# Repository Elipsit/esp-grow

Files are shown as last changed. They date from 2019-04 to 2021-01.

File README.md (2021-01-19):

# esp-grow
## Project Description
This was a project designed to get fimilar with the ESP8266 and ESP32 chipset.

## esp-grow
### This was an esp8266 based automatic plant monitor system.
The system will monitor the capacitive soil sensor, tenperature and humidity and activate the water pump accordingly.
The system hosts its own webpage to give the user status of the plants progress.

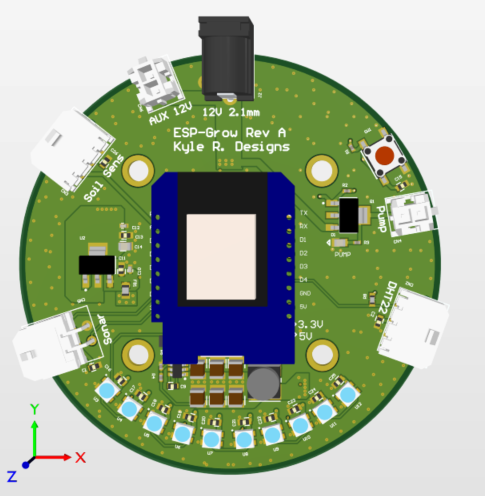
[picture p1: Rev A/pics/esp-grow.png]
esp-grow


custom soil sensor
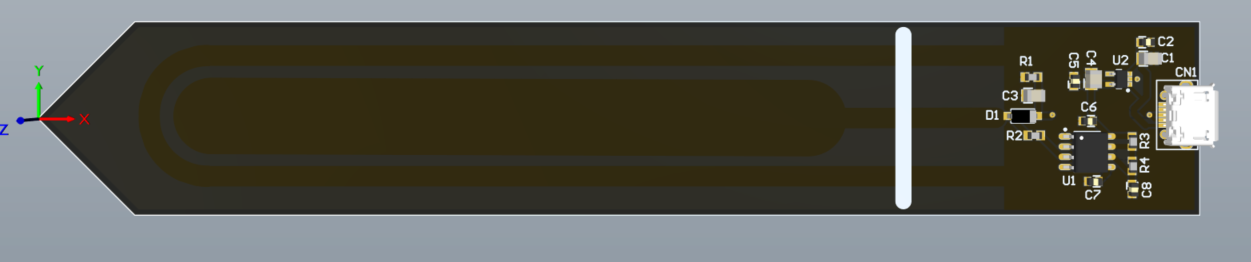
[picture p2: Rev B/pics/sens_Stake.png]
sens_stake


## Design Files
### Electrical Design Files
This project contains the Altium Designer schematic and pcb files, wiring diacrams and code for an esp8266 based indoor plant monitoring system.

This system is comprised of three main blocks:
1) Wemos D1 - ESP-12F; I really like working with this form factor since it has an esp8266 with a breadboard header and a CH340G
2) ESP-Grow_OLED_Rev_A: custom 2 layer pcb with a generic SSD1306 128x64 I2C monochrome OLED screen and a tack button seated under the screen.      Basically a screen button.
3) ESP-Grow_OLED_Main_A: The motherboard. A custom 4 Layer pcb with all the connectors, power rails and leds.

Update:
-DHT22 library has an error with ESP8266 and ESP32, changing to DHT11 for project sensor

###Current Progress: 5/18/2019
Project is functional. Rev A is retired.

## esp32-grow
### This was an esp32 based automatic plant monitor system.
This system was designed to monitor up to 50 plants at a time and upload the data to google firebase.
The device measures 50 capacitive soil sensors, air temperature, humidity and a single pH probe.

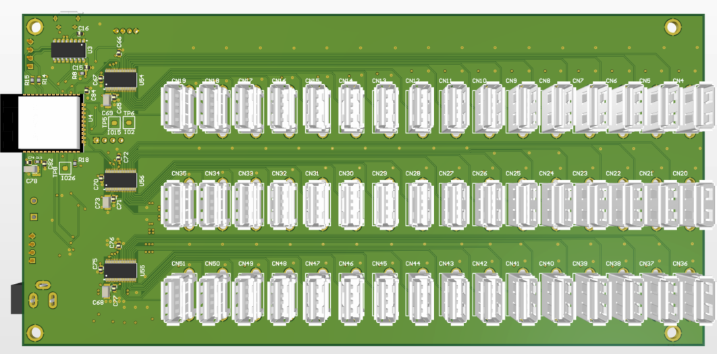
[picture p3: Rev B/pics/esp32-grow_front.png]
esp32-grow


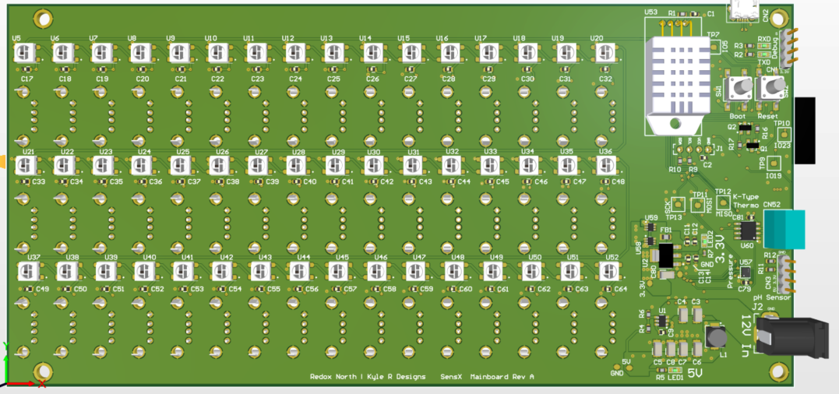
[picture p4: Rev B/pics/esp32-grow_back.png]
esp32-grow


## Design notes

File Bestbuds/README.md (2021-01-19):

# BestBuds
 Best Buds growing platform for ESP32

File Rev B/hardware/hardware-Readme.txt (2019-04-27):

All pcb design was done in Altium Designer 17 and Nexus

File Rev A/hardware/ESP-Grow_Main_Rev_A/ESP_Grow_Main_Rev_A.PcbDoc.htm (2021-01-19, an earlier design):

Reporting Options

# File in Previous Format

Date | : | 1/18/2021
Time | : | 10:08:27 PM
Filename | : | C:\github\esp-grow\Rev A\hardware\ESP-Grow_Main_Rev_A\ESP_Grow_Main_Rev_A.PcbDoc

Version | Warning

This file was generated by an earlier version of the software

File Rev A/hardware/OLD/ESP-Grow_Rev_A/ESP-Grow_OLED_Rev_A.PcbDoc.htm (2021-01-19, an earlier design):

Reporting Options

# File in Previous Format

Date | : | 6/29/2020
Time | : | 7:53:46 PM
Filename | : | C:\github\esp-grow\Rev A\hardware\OLD\ESP-Grow_Rev_A\ESP-Grow_OLED_Rev_A.PcbDoc

Version | Warning

This file was generated by an earlier version of the software

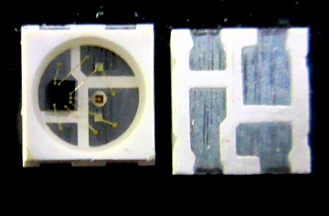
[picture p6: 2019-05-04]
Rev B/hardware/Datasheets/RGB/sk6812-sk6814-smd3535-1.snapshot.1/Capture0.PNG

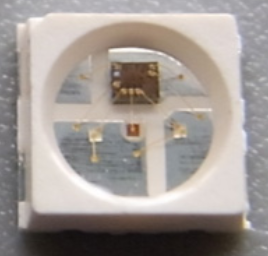
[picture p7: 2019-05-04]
Rev B/hardware/Datasheets/RGB/sk6812-sk6814-smd3535-1.snapshot.1/Capture2.PNG

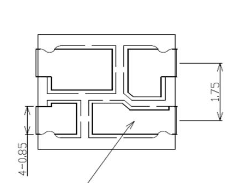
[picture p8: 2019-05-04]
Rev B/hardware/Datasheets/RGB/sk6812-sk6814-smd3535-1.snapshot.1/Capture1.PNG

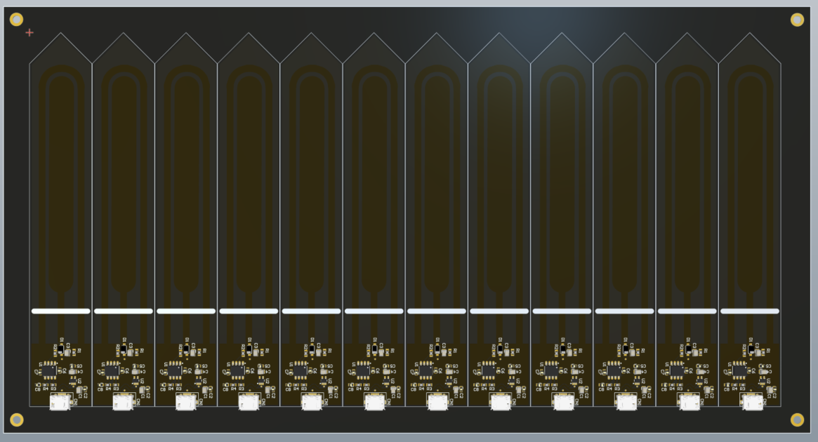
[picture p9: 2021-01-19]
Rev B/pics/Sens_Stake_panel.png

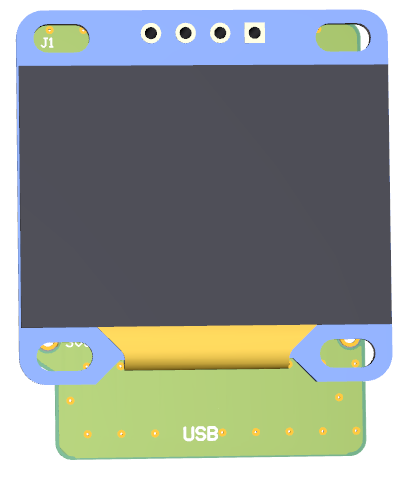
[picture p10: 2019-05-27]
Rev B/visio/ESP-Grow_OLED_Rev_A.1.PNG

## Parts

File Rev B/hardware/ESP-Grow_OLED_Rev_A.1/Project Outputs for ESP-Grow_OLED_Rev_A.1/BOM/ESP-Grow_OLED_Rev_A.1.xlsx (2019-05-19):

Line # | Name | Description | Designator | Quantity | Manufacturer 1 | Manufacturer Part Number 1 | Manufacturer Lifecycle 1 | Supplier 1 | Supplier Part Number 1 | Supplier Unit Price 1 | Supplier Subtotal 1
 | 0.1uF | CAP CER 0.1UF 50V 10% X7R 0805 | C1 | 1
 | J/Wemo_ESP_Shield | Wemo Mini Shield for ESP-12 | CN1 | 1
 | OLED 0.96" | SSD1306 I2C OLED 0.96" | J1 | 1
 | 10K | RES 10K OHM 1/10W 1% 0603 SMD | R1, R2, R3 | 3
 | PTS645SM43SMTR92 LFS | SWITCH TACTILE SPST-NO 0.05A 12V | SW1 | 1

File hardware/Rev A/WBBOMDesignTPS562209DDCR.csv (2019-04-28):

Part | Manufacturer | Part Number | Quantity | Price ($) | Footprint (mm²) | Description
Cin | TDK | C2012X6S1C226M125AC | 1 | 0.26 | 6.75 | Cap: 22 µF Total Derated Cap: 5.5 µF VDC: 16 V ESR: 2.05 mΩ Package: 0805
Rfbb | Yageo | RC0201FR-0710KL | 1 | 0.01 | 2.08 | Resistance: 10 kΩ Tolerance: 1.0% Power: 50 mW
U1 | Texas Instruments | TPS562209DDCR | 1 | 0.4 | 10.47
Cbst | Kemet | C0603C104Z3VACTU | 1 | 0.01 | 4.68 | Cap: 100 nF Total Derated Cap: 100 nF VDC: 25 V ESR: 1 mΩ Package: 0603
Cout | TDK | C1608X5R1A226M080AC | 1 | 0.13 | 4.68 | Cap: 22 µF Total Derated Cap: 4.5 µF VDC: 10 V ESR: 3.71 mΩ Package: 0603
L1 | Bourns | SRN6045-4R7Y | 1 | 0.2 | 64 | L: 4.7 µH DCR: 37.6 mΩ IDC: 3 A
Rfbt | Yageo | RC0201FR-0756K2L | 1 | 0.01 | 2.08 | Resistance: 56.2 kΩ Tolerance: 1.0% Power: 50 mW

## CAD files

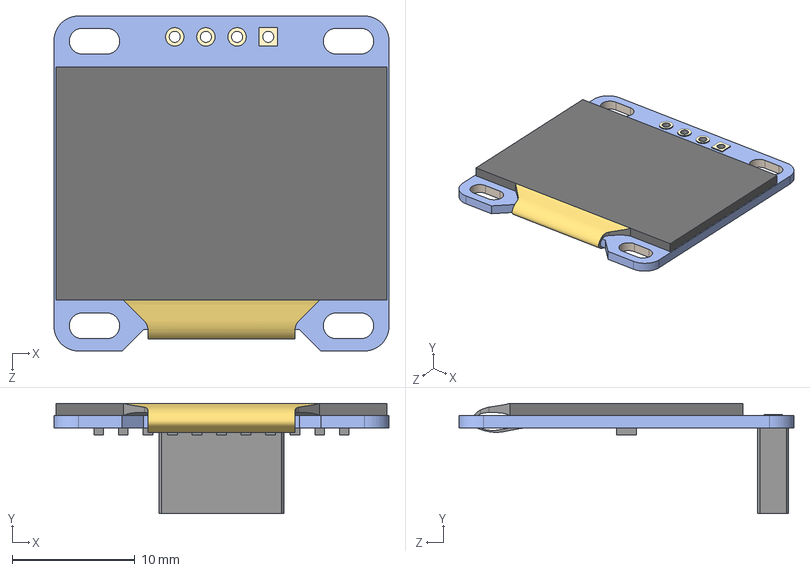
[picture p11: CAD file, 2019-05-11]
Rev B/hardware/Datasheets/OLED_27x27_r2.STEP
27.3 x 9.00 x 27.3 mm

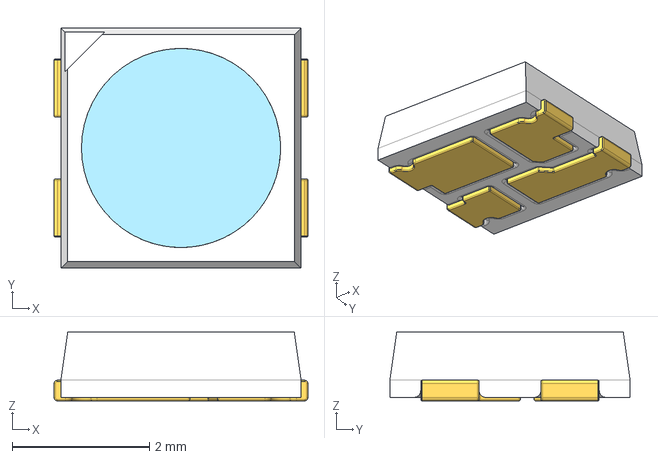
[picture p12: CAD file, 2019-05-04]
Rev B/hardware/Datasheets/RGB/sk6812-sk6814-smd3535-1.snapshot.1/SMD3535 RGB.stp
3.70 x 3.50 x 1.00 mm

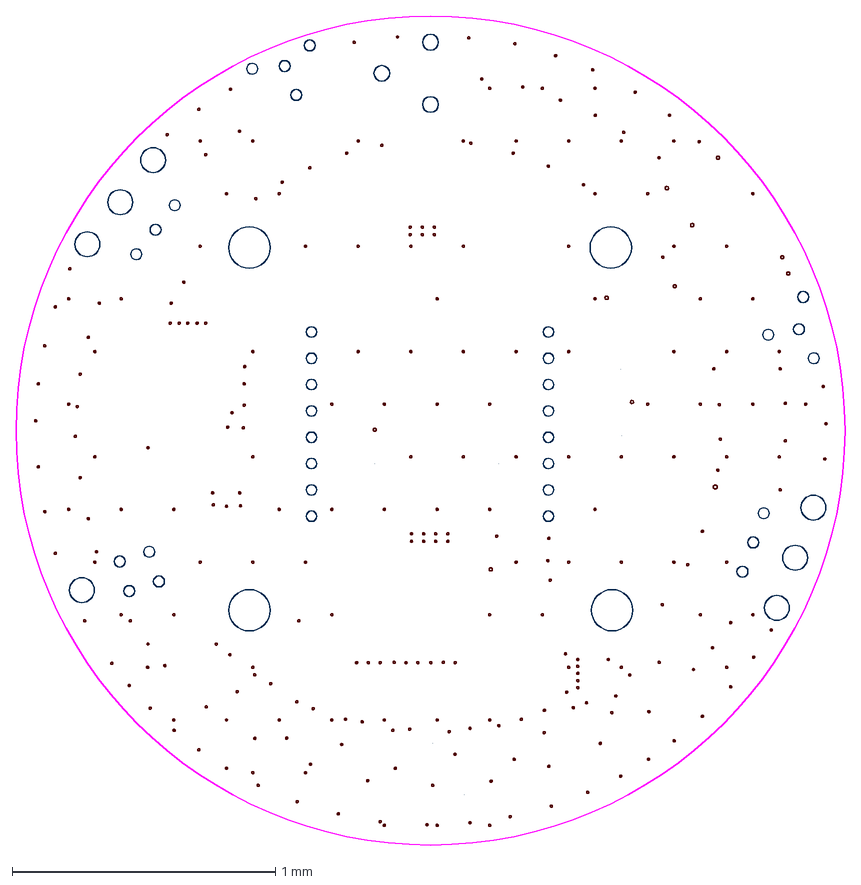
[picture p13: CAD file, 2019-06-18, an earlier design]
Rev A/mechanical/ESP_Grow_Main_Rev_A_Keepout.DXF
3.15 x 3.15 mm

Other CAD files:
Rev A/hardware/ESP-Grow_Main_Rev_A/ESP_Grow_Main_Rev_A.DXF

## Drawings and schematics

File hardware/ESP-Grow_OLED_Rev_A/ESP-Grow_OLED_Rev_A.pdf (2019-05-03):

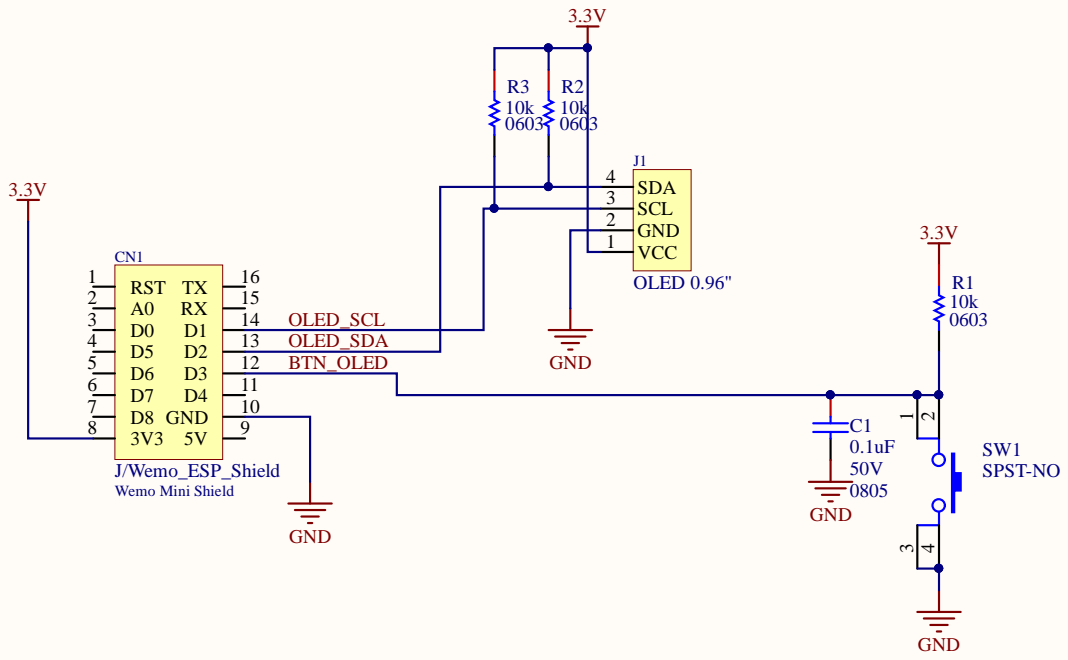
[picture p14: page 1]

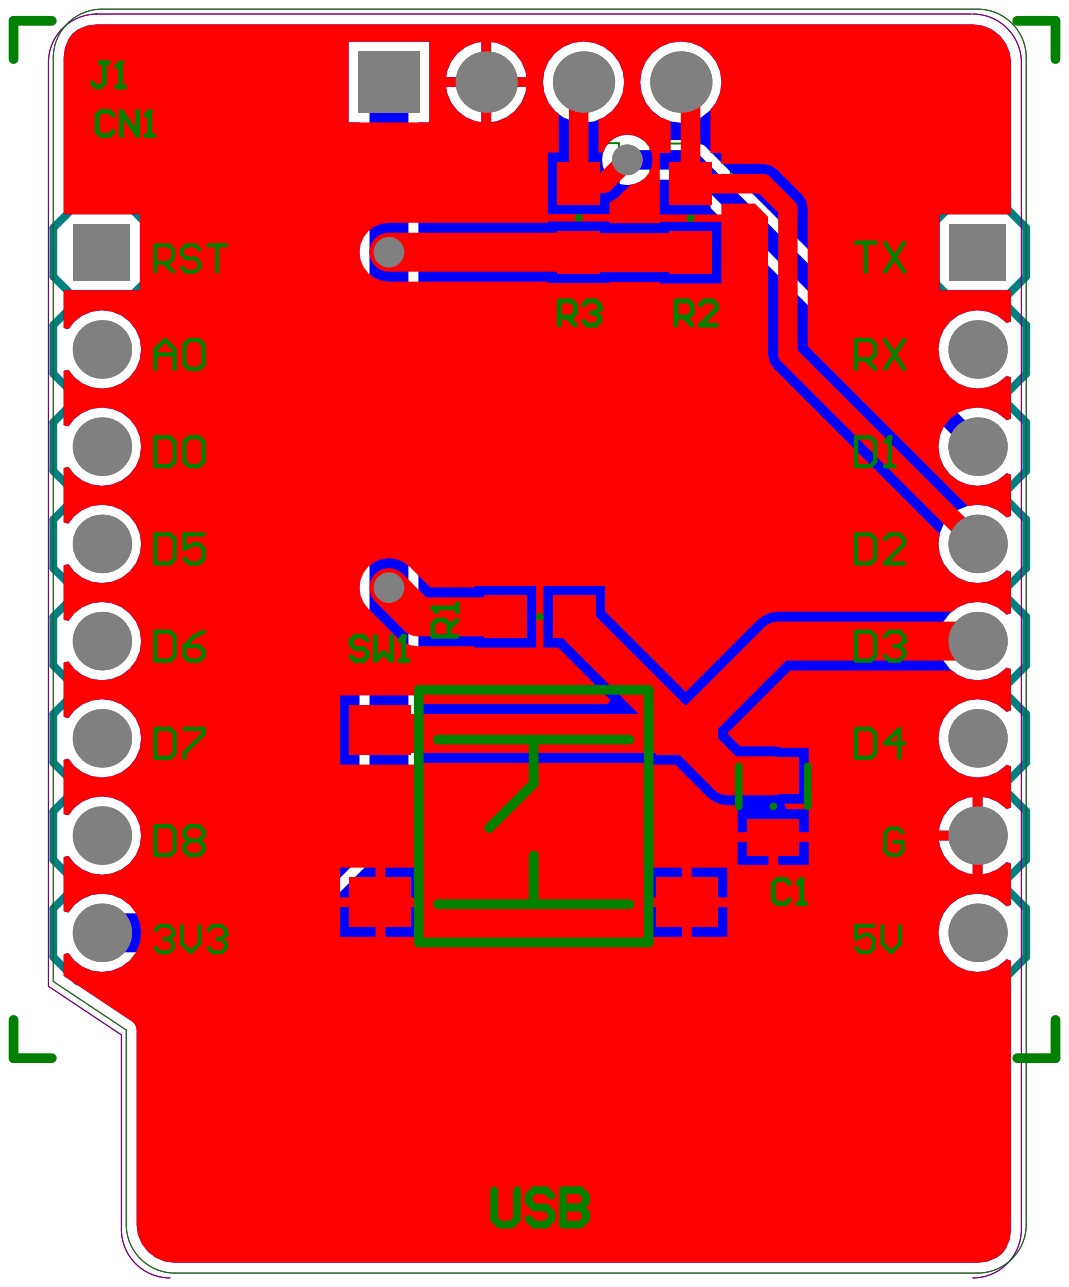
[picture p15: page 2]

Line # | Name | Description | Designator | Quantity | Manufacturer 1 | Manufacturer Part Number 1 | Manufacturer Lifecycle 1 | Supplier 1 | Supplier Part Number 1 | Supplier Unit Price 1 | Supplier Subtotal 1
| 0.1uF | CAP CER 0.1UF 50V 10% X7R 0805 | C1 | 1
| 10K | RES 10K OHM 1/10W 1% 0603 SMD | R1, R2, R3 | 3
| OLED 0.96" | SSD1306 I2C OLED 0.96" | J1 | 1
| PTS645SM43S MTR92 LFS | SWITCH TACTILE SPST-NO 0.05A 12V | SW1 | 1
| J/Wemo_ESP_ Shield | Wemo Mini Shield for ESP-12 | CN1 | 1

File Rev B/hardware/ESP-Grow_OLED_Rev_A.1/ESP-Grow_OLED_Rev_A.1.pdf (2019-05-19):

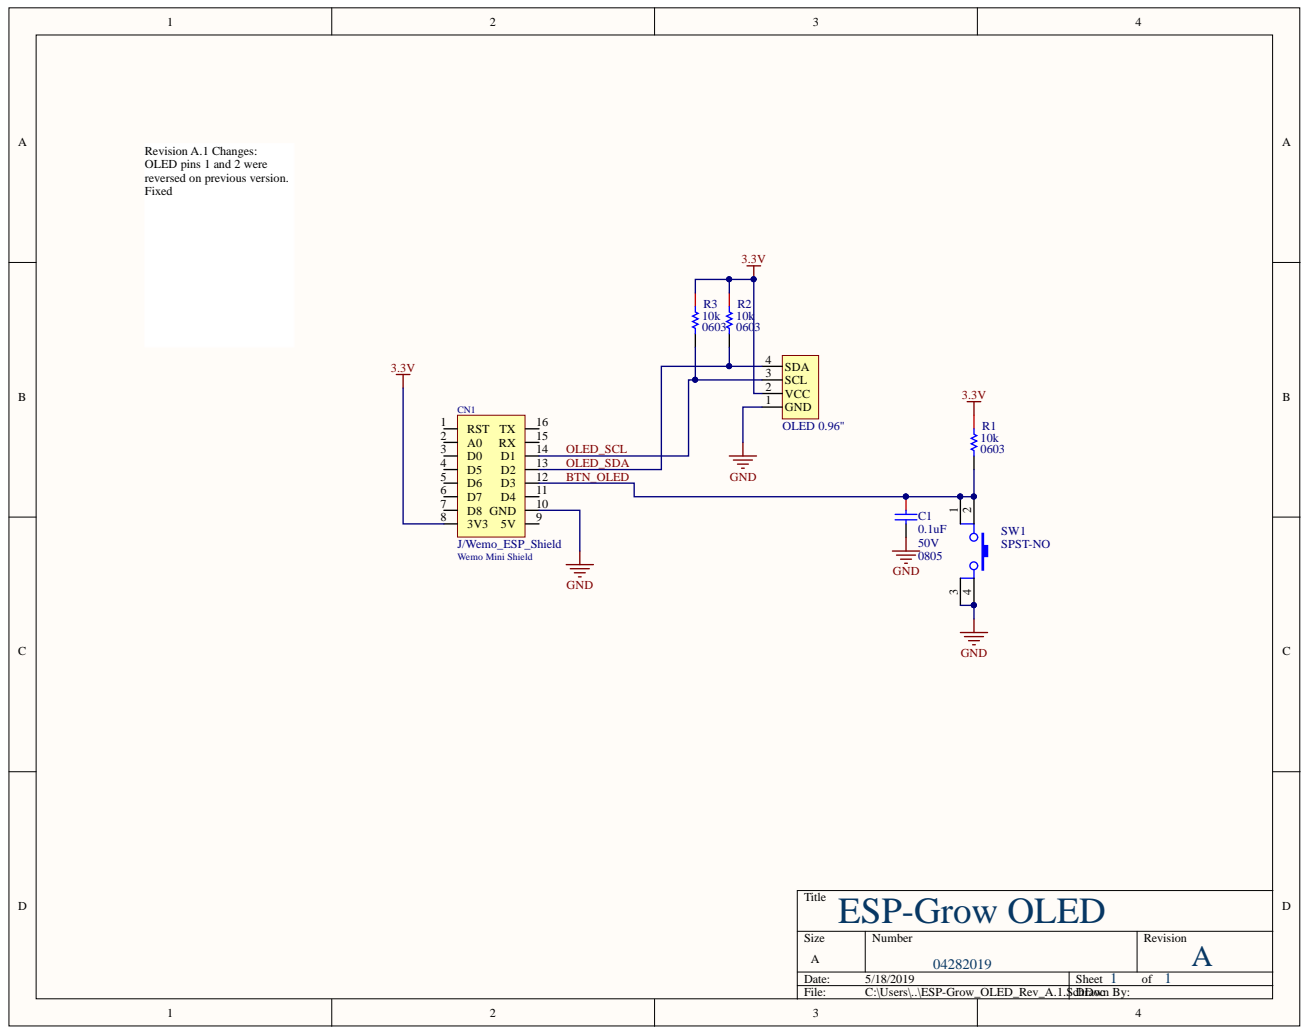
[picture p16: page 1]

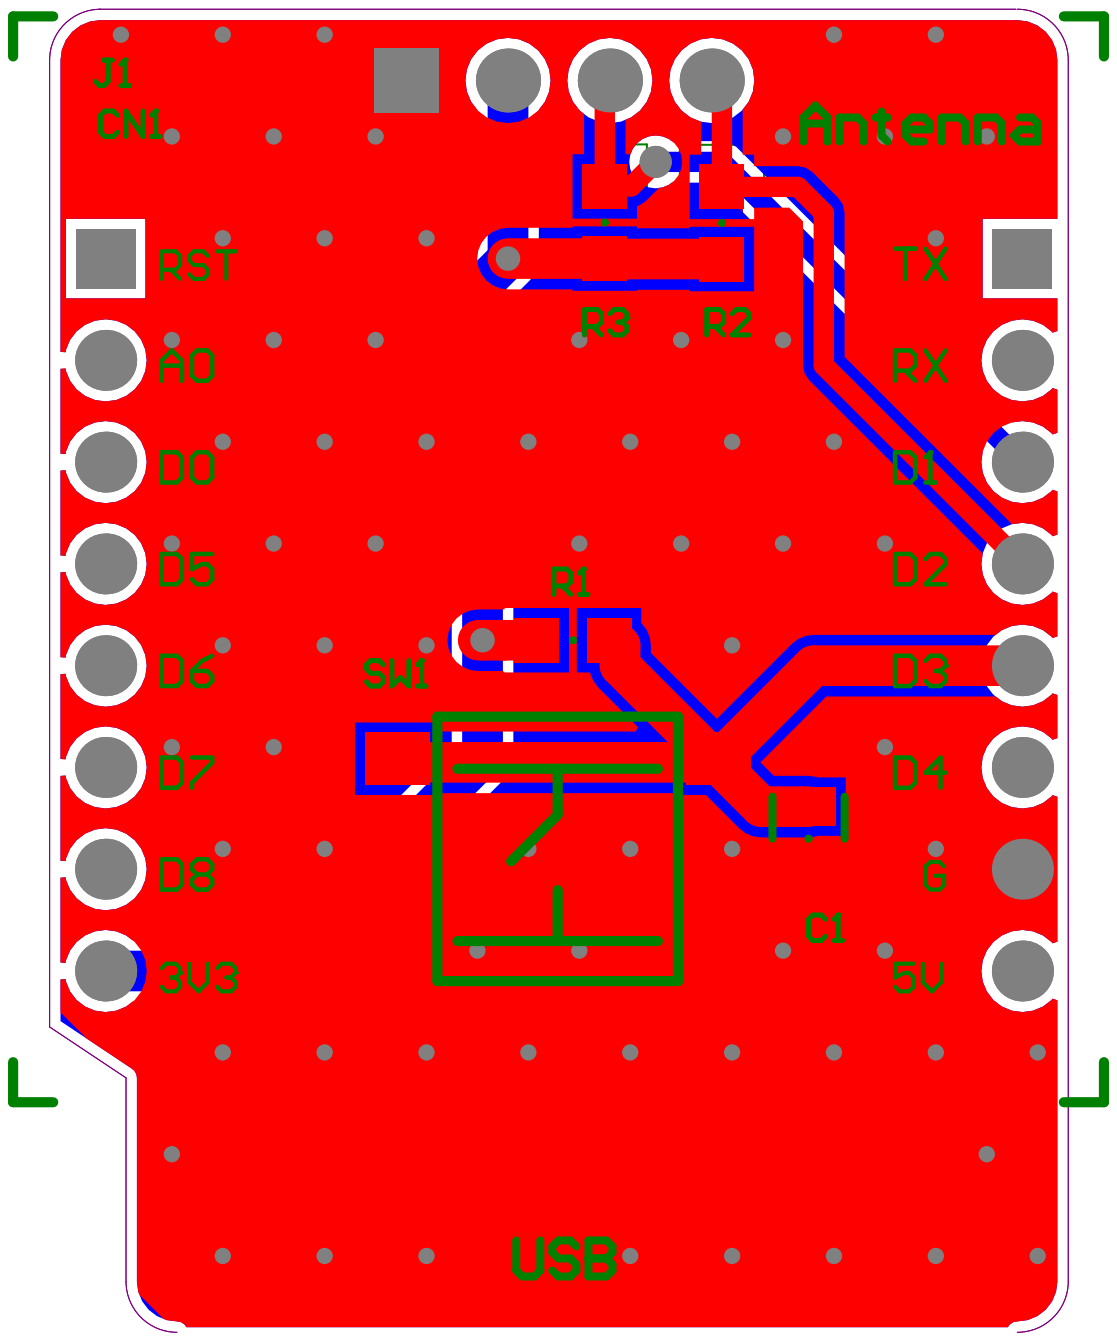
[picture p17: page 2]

# Board Stack

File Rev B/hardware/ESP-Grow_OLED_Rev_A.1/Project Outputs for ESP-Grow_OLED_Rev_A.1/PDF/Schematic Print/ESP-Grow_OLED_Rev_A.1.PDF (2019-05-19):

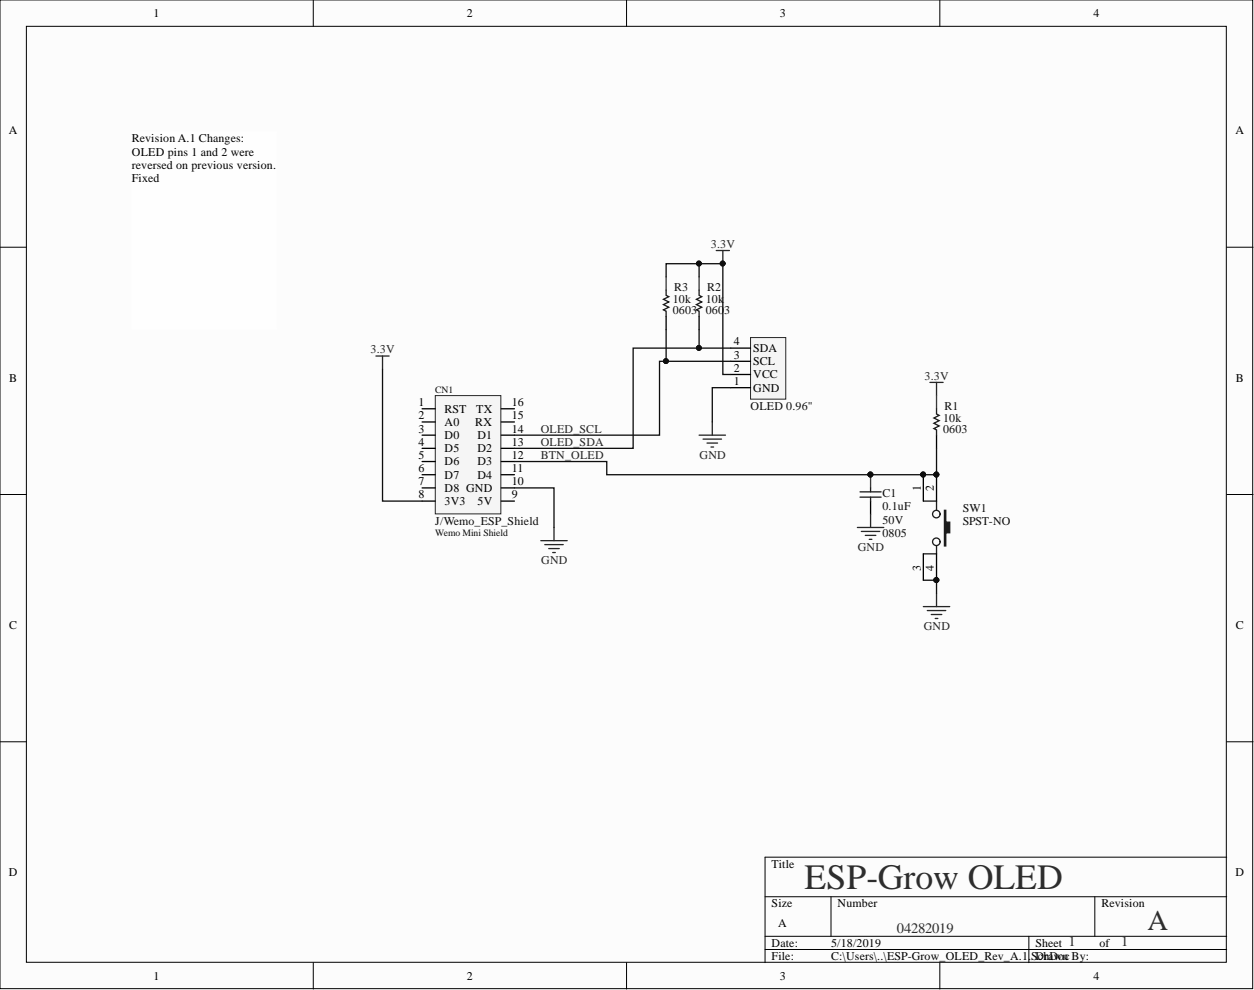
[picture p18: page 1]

4 | | 1 3 O L E D _SD A
5 | 1 2 BT N _ O L E D G N D
8 | | 9 iel d

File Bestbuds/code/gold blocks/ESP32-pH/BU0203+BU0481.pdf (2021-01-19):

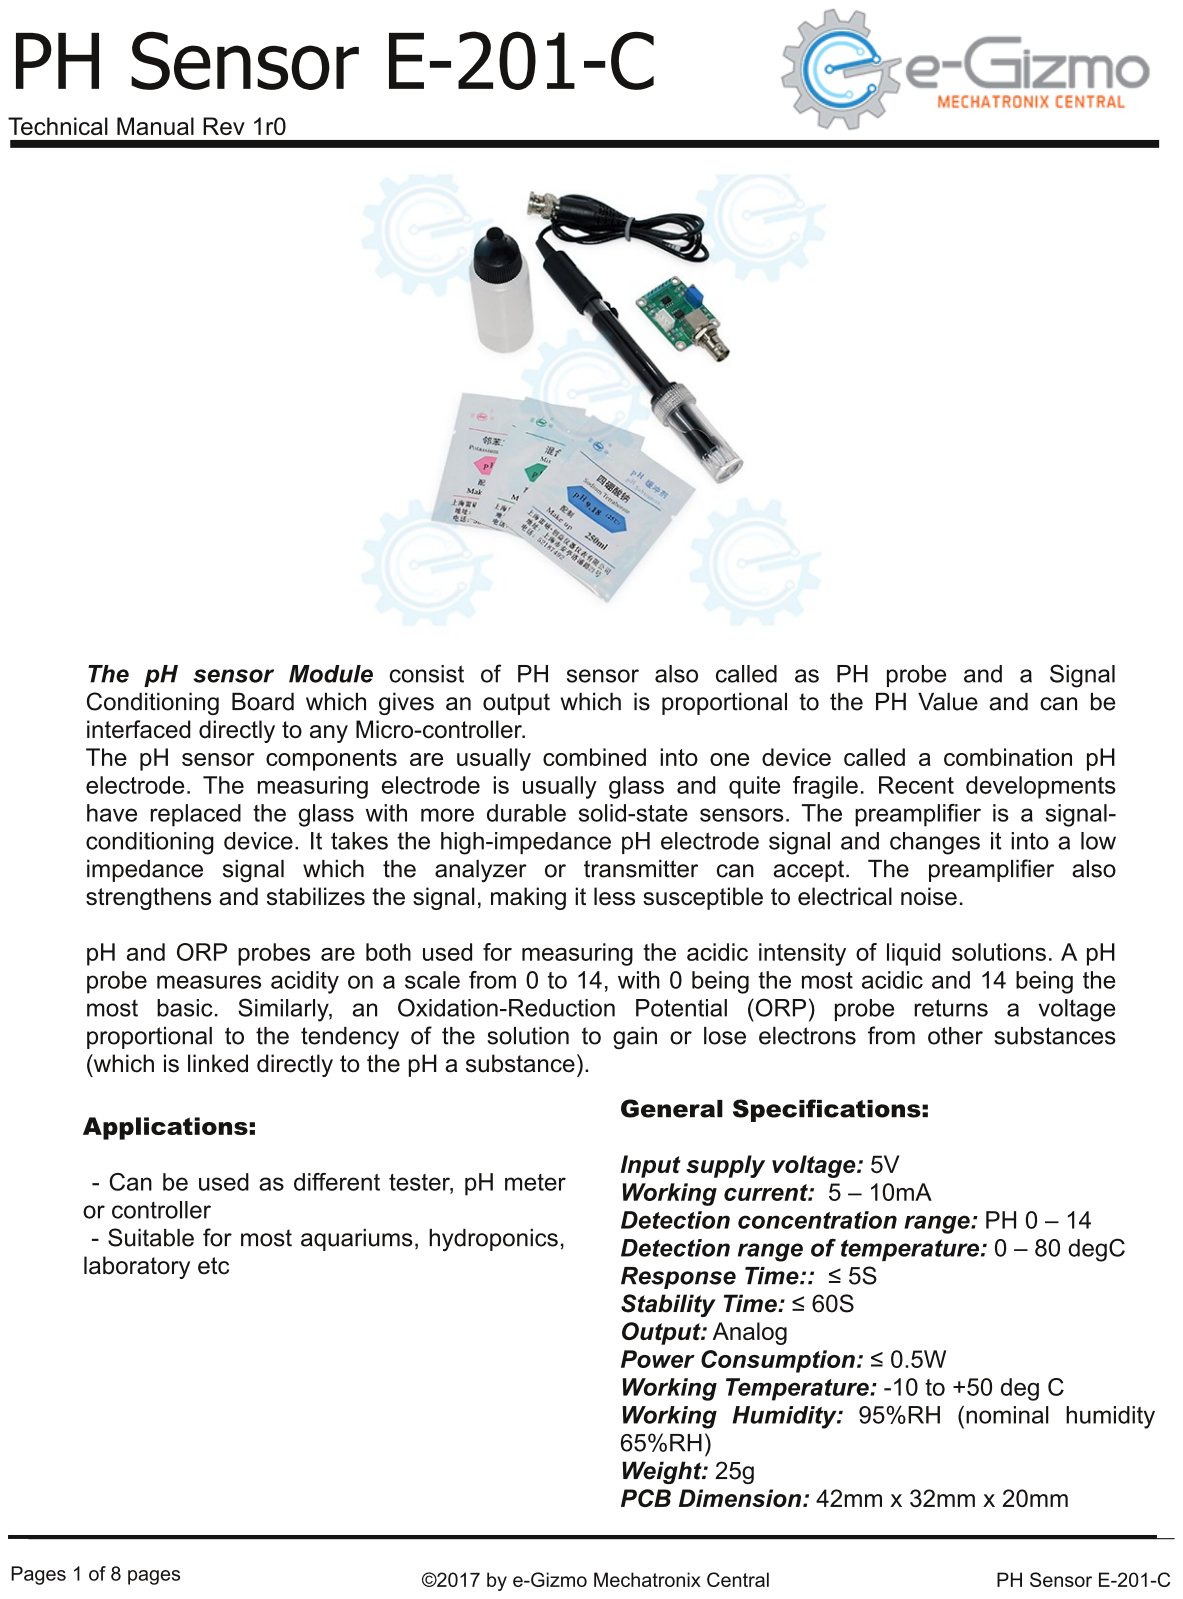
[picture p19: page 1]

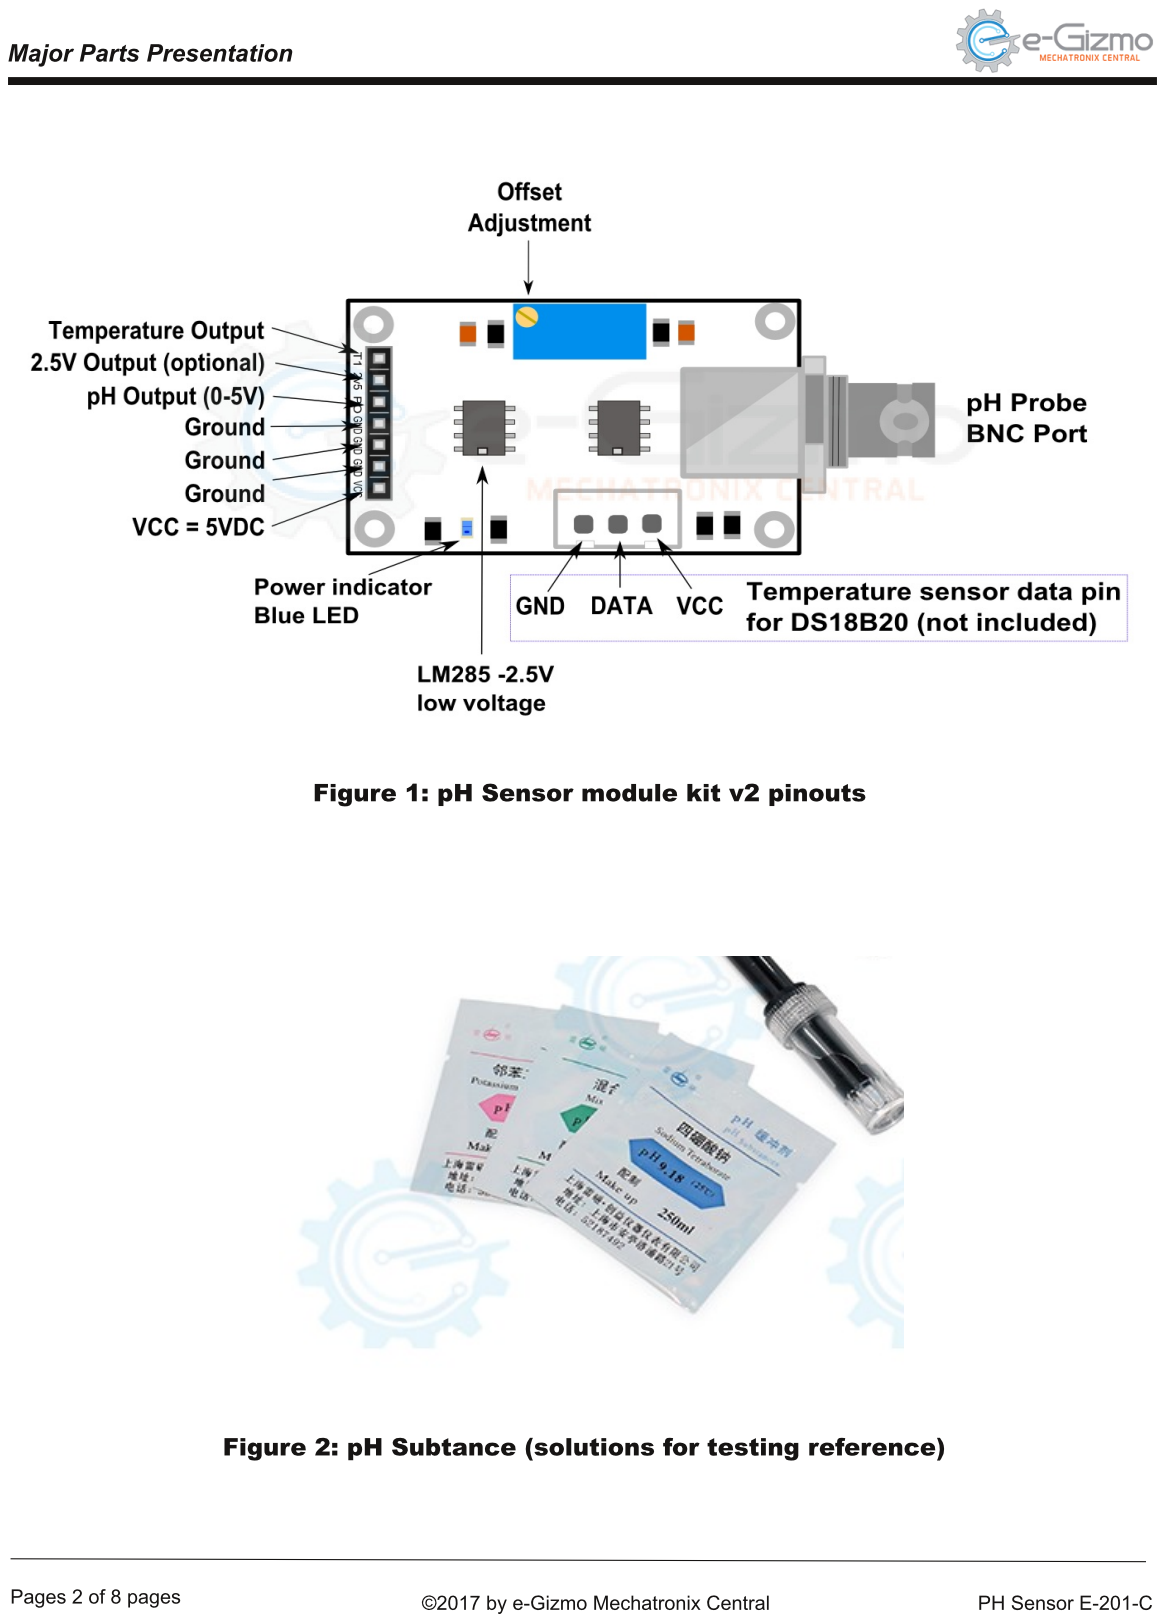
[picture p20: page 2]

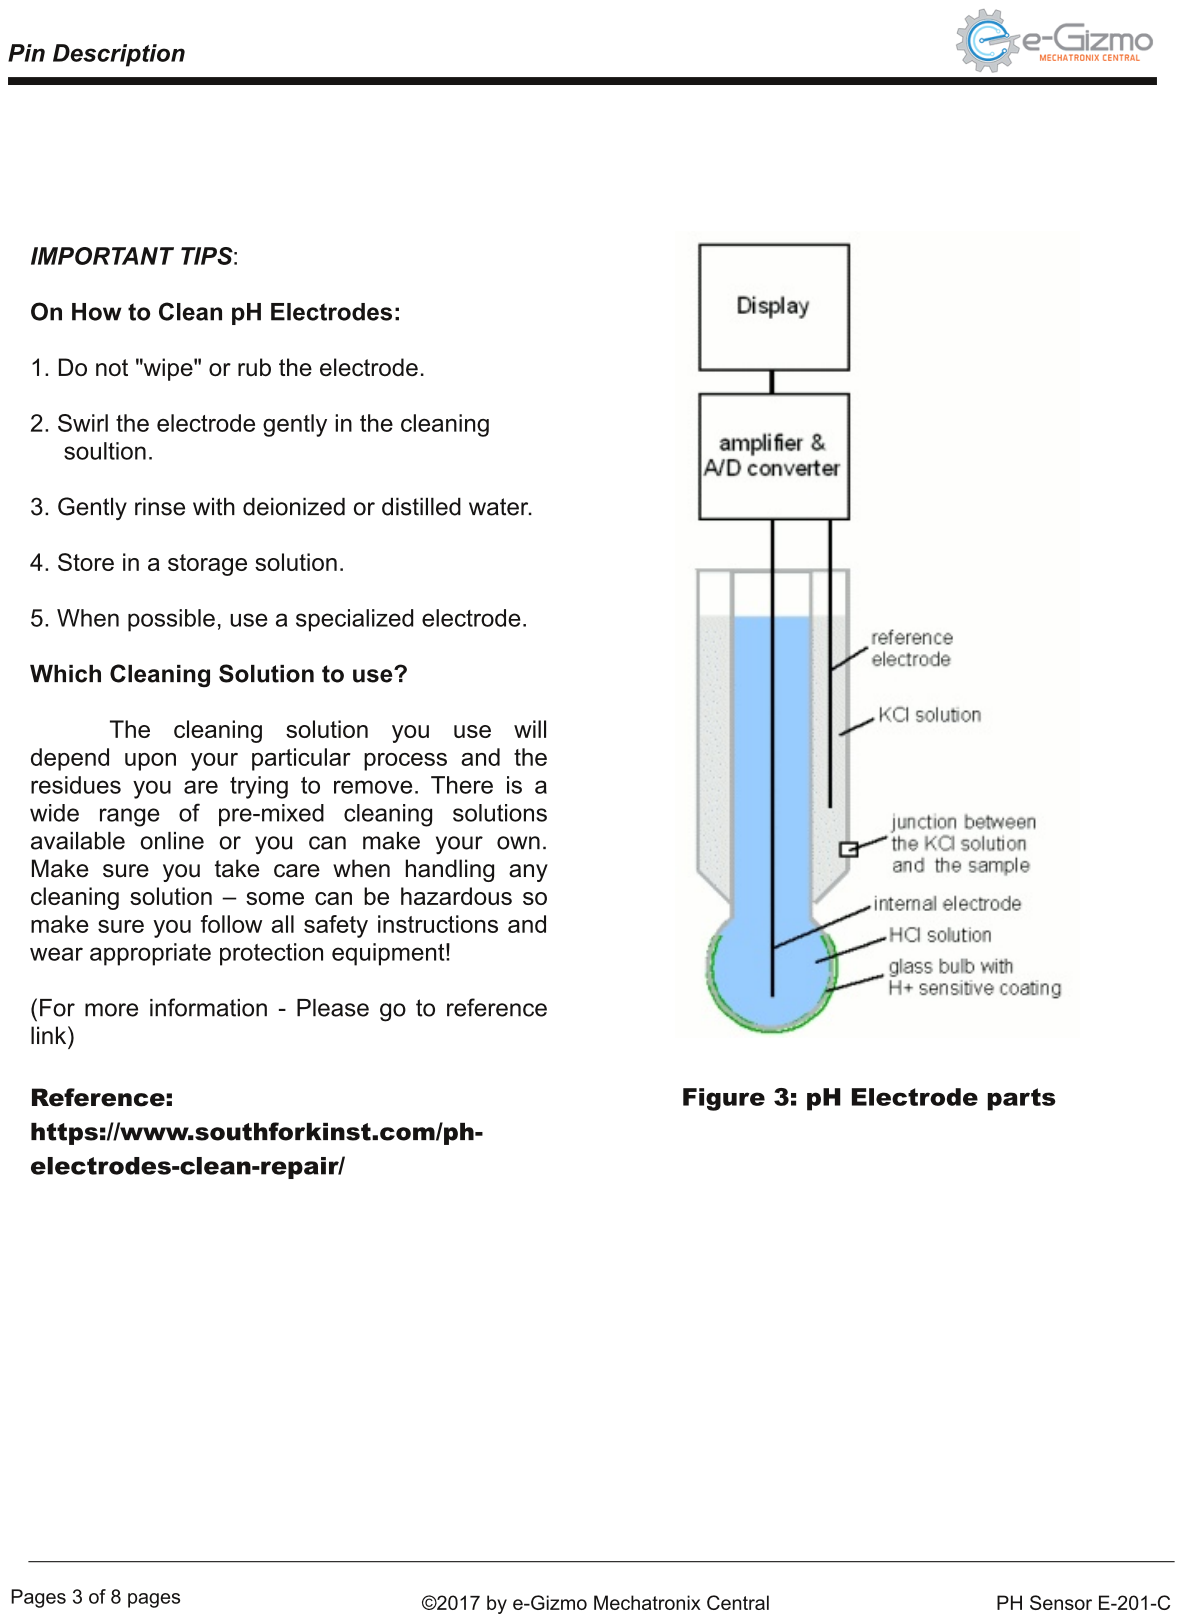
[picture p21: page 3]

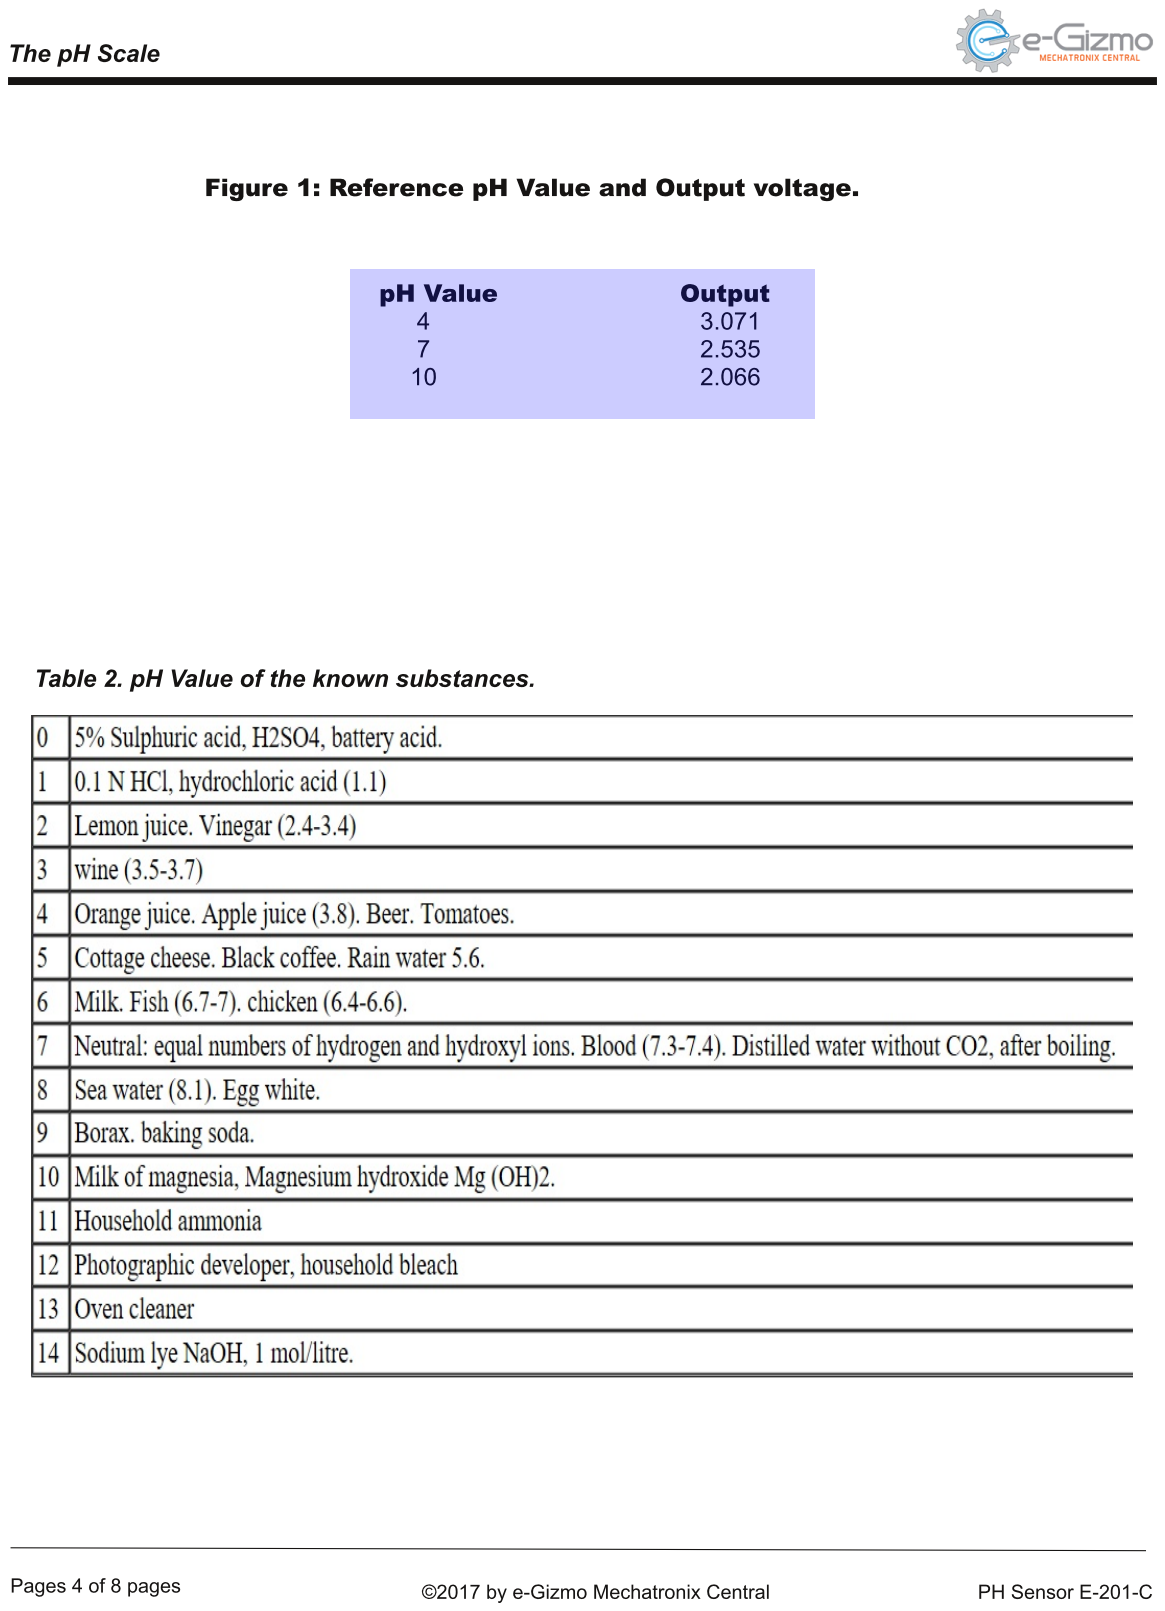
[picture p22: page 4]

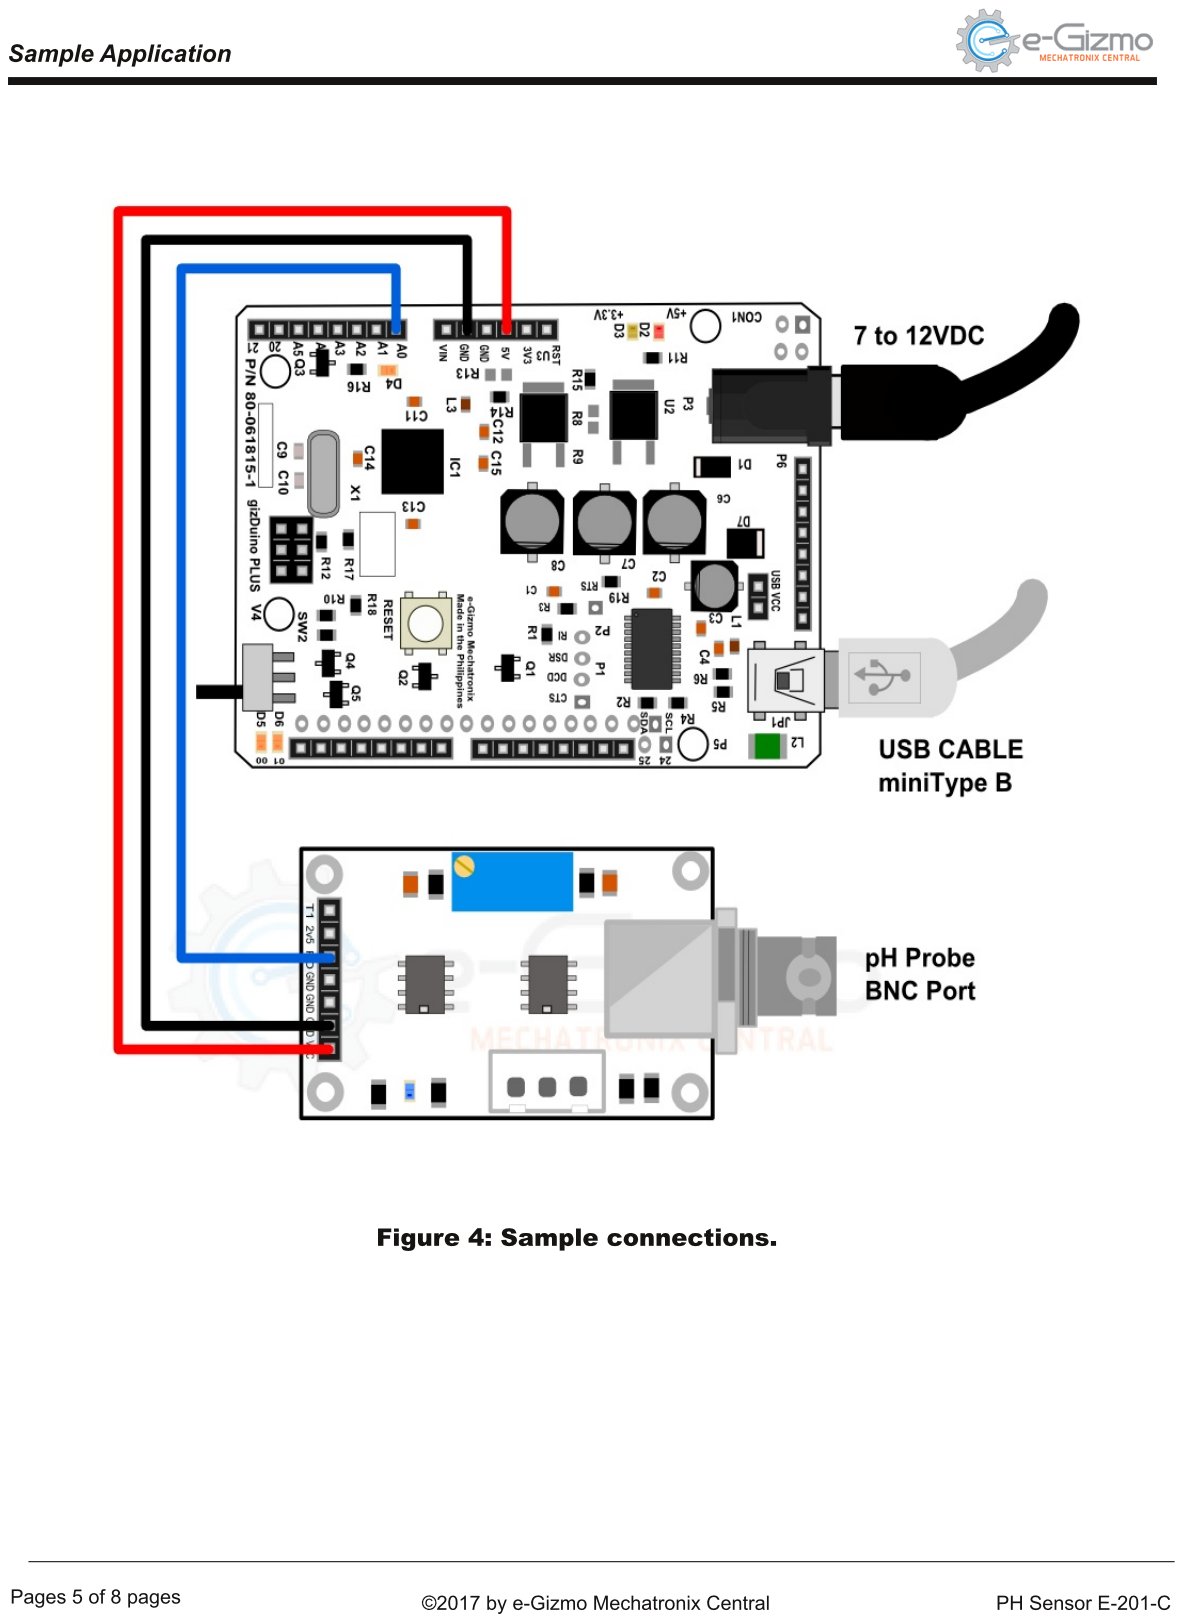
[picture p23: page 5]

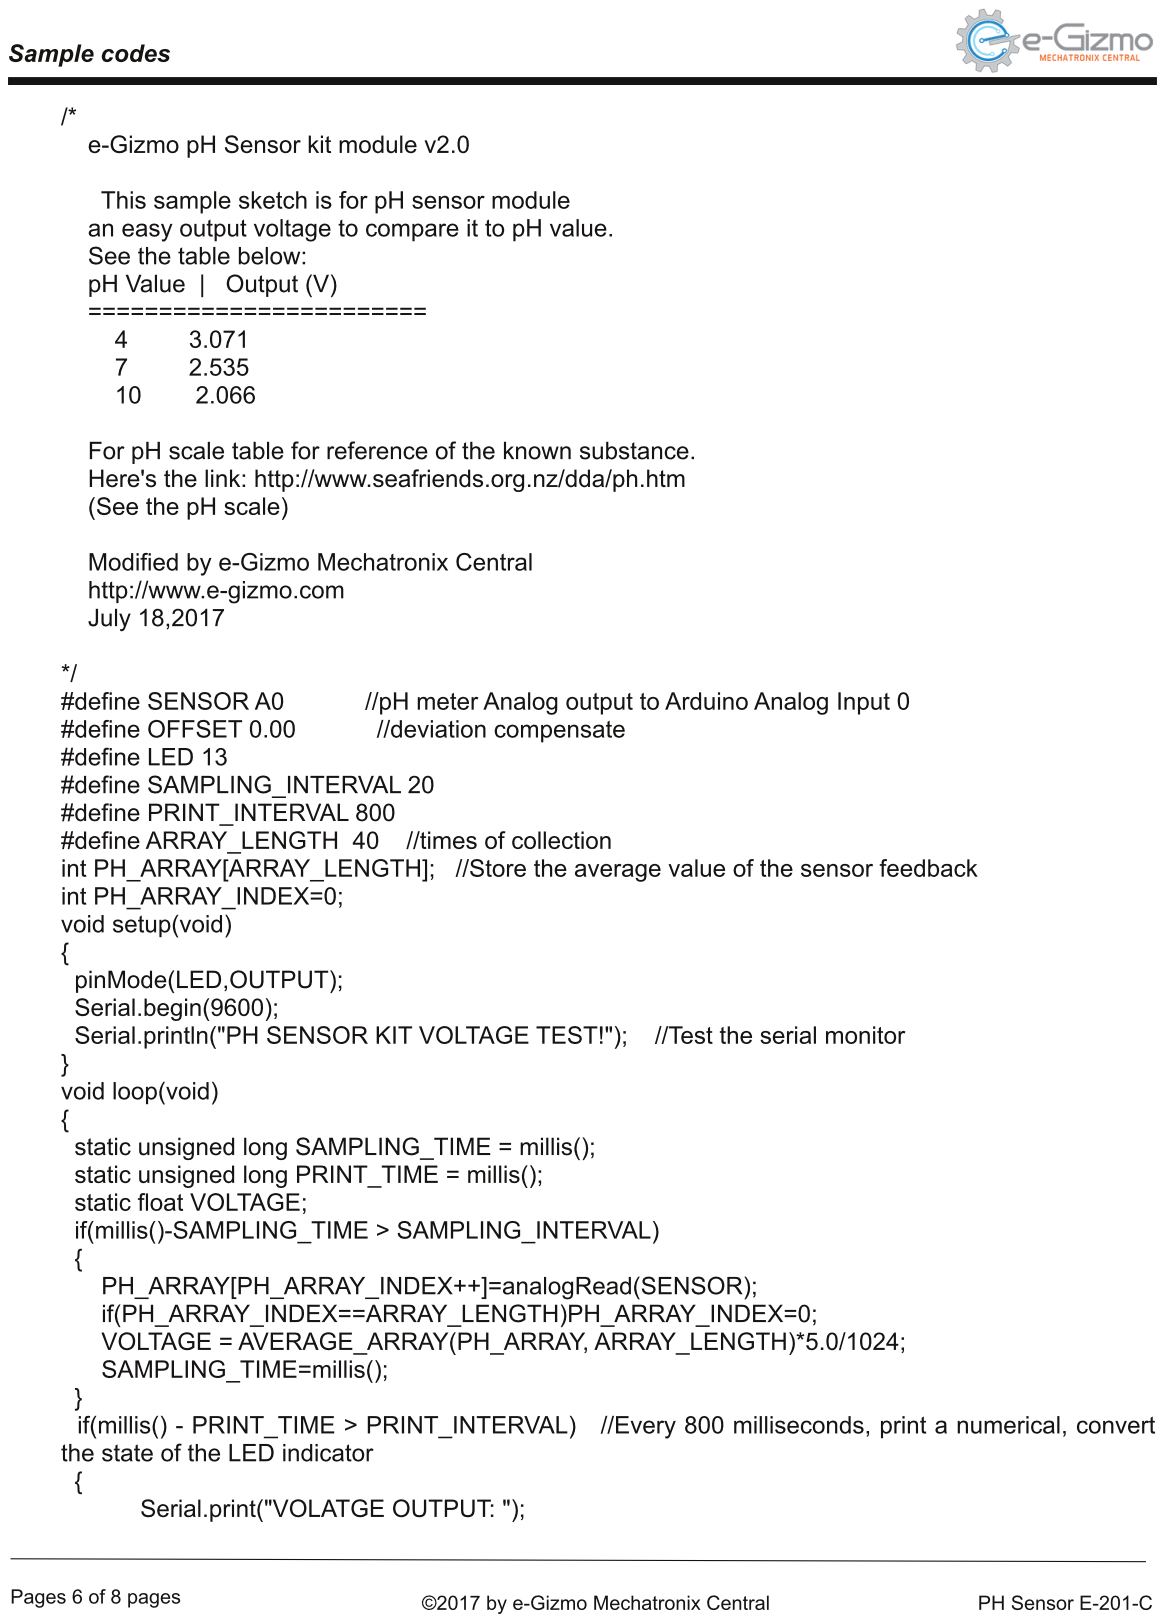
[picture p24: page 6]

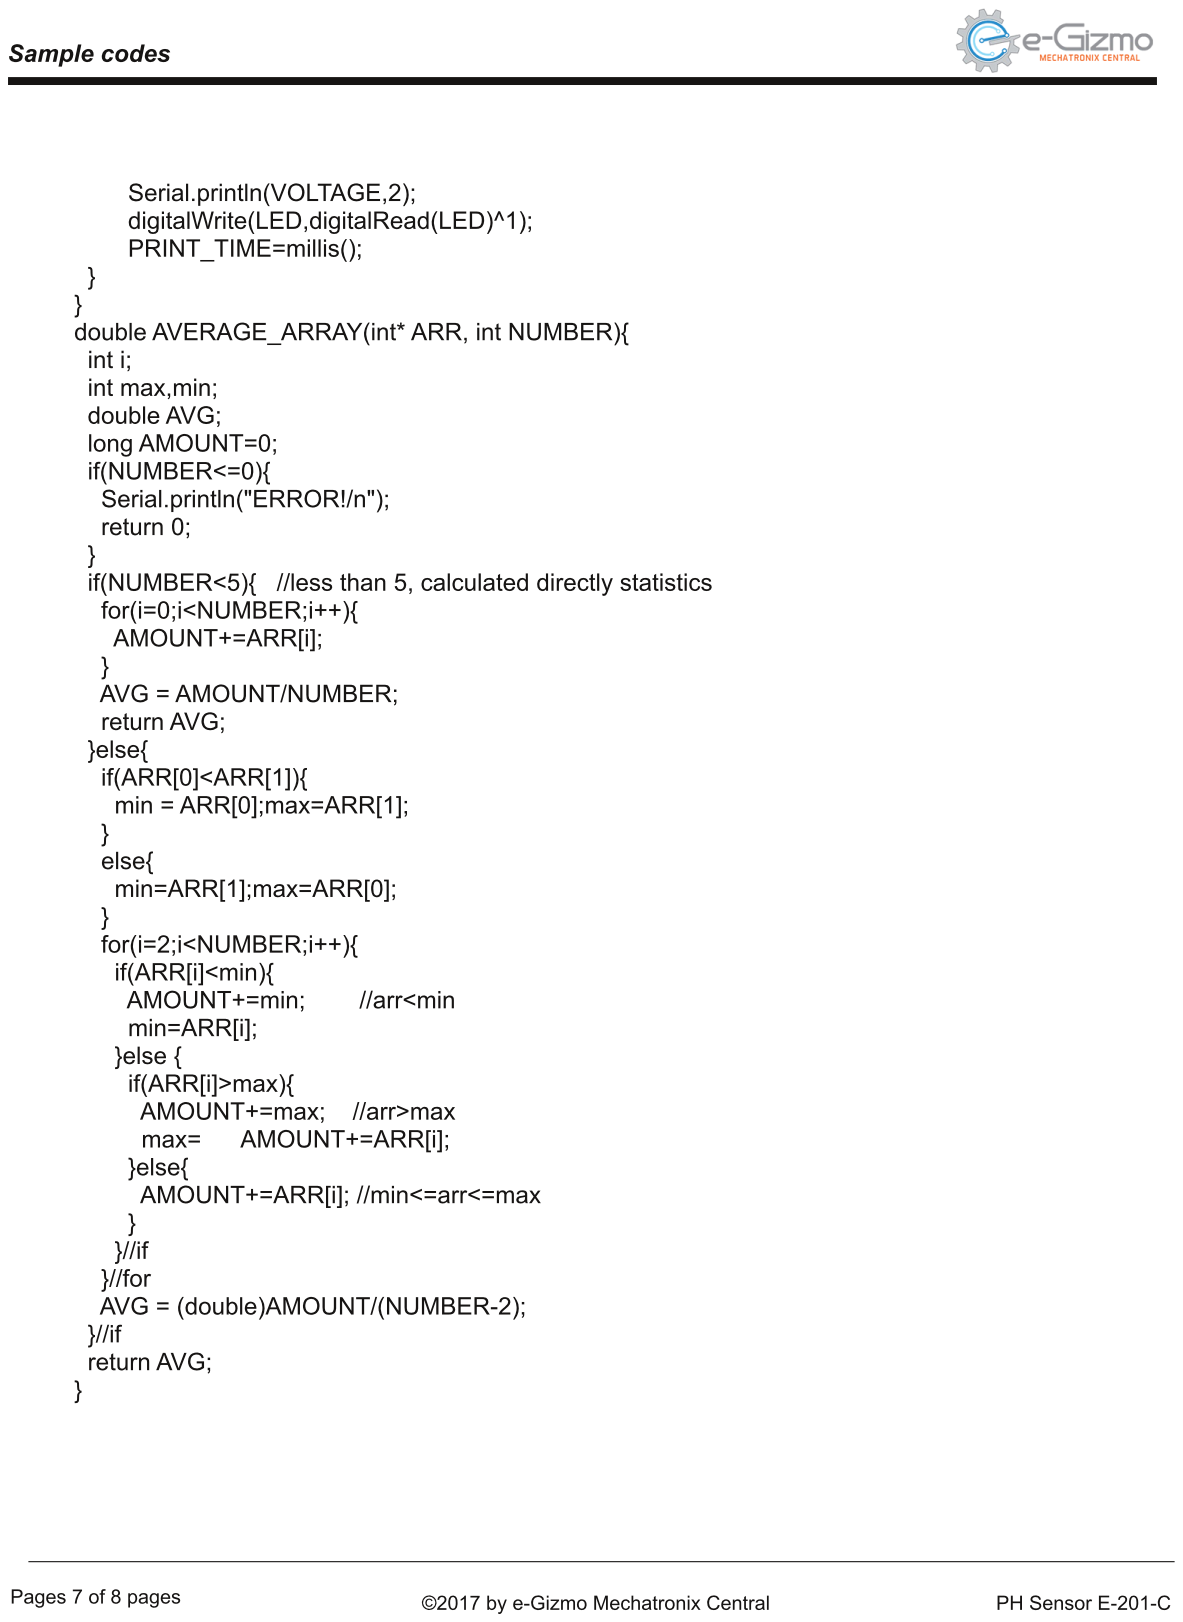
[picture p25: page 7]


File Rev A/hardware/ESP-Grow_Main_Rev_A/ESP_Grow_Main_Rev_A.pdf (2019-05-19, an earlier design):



https://webench.ti.com/appinfo/webench/scripts/SDP.cgi?ID=B83D159DABBA9445



Line # | Name | Description | Designator | Quantity | Manufacturer 1 | Manufacturer Part Number 1 | Manufacturer Lifecycle 1 | Supplier 1 | Supplier Part Number 1 | Supplier Unit Price 1 | Supplier Subtotal 1
| 10uF | 10uF 1210 25V | C3, C4, C5, C6, C7, C8 | 6 TDK | | C3225JB1E106K250AA | Volume Production | Digi-Key | 445-11850-1-ND
| 0.1uF | 0.1uF 0603 16V | C9 | 1 | KEMET | C0603C104K4RAC7867 | Not Recommended for New Design | Digi-Key | 399-1096-2-ND | 0.02167 | 86.68
| 0.1uF | 0.1uF 0402 25V | C10, C12 | 2 Taiyo | | TMK105BJ104KV-F | Unknown | Digi-Key | 587-1456-1-ND | 0.1 | 0.2
| 1uF | 1uF 0603 25V | C11, C13, C15, C16, C17, C18, C19, C20, C21, C22, C23, C24, C25 | 13 TDK | | CGA3E1X7R1E105K080AC | Volume Production | Digi-Key | 445-6931-1-ND | 0.123 | 1.6
| 10uF | 10UF 25V X6R 0805 | C14 | 1 | Murata | GRM21BC81E106ME51L | Volume Production | Digi-Key | 490-10503-1-ND | 0.34 | 0.34
| J/Wemo_ESP_ Shield | Wemo Mini Shield for ESP-12 | CN1 | 1
| DHT22 | Molex Microfit 1x3 90deg Header | CN2 | 1 | Molex | 0436500304 | Volume Production | Digi-Key | WM1876-ND
| SOIL SENS | Molex Microfit 1x3 90deg Header | CN3 | 1 | Molex | 0436500304 | Volume Production | Digi-Key | WM1876-ND
| PUMP | Molex Microfit 1x2 Vert Header | CN4 | 1 | Molex | 0430450227 | Volume Production | Digi-Key | WM10657-ND | 0.84 | 0.84
| SONAR | Molex Microfit 2x2 90deg Header | CN5 | 1 | Molex | 43045-0400 | Volume Production | Digi-Key | WM1814-ND | 1.42 | 1.42
| AUX 12V | Molex Microfit 1x2 Vert Header | CN6 | 1 | Molex | 43045-0227 | Volume Production | Digi-Key | WM10657-ND | 0.84 | 0.84
| D/LEDR/0805 | Red 625nm LED Indication -Discrete 2V 0805 | D1 | 1 | Wurth Electronics | 150080RS75000 | Volume Production | Digi-Key | 732-4984-6-ND | 0.17 | 0.17
| D/LEDB/0603 | | D2, D3 | 2 Everlight | | EAST16084BA8 | Unknown | Digi-Key | 1080-1562-6-ND
| 600 Ohm @ 100MHz | 600 OHM 0805 2.0A | FB1 | 1 | Wurth Electronics | 742792040 | Volume Production | Digi-Key | 732-1620-1-ND | 0.22 | 0.22
| 12V 2.1mm | 2.1 mm barrel jack | J2 | 1 | CUI | PJ-002AH | Volume Production | Digi-Key | CP-002AH-ND | 0.74 | 0.74
| 4.7uH | FIXED IND 4.7UH 3A 37.6 MOHM SMD | L1 | 1
| DMP6023LE-13 | MOSFET P-CH 60V 7A SOT223 | Q1 | 1 | Diodes | DMP6023LE-13 | Volume Production | Digi-Key | DMP6023LE-13DICT-ND
| 10K | 10K 0402 | R1, R2, R6 | 3 Samsung | | RC1005F103CS | Volume Production | Digi-Key | 1276-3431-1-ND | 0.02 | 0.2
| 1K | 1K 0402 | R3 | 1 | Yageo | RC0402FR-071KL | Volume Production | Digi-Key | 311-1.00KLRCT-ND | 0.1 | 0.1
| 56.2K 1% | 56.2K 1% 0402 | R4 | 1 | Panasonic | ERJ2RKF5622X | Volume Production | Digi-Key | P56.2KLCT-ND | 0.1 | 0.1
| 470 | 470 0402 | R5 | 1 | Panasonic | ERJ-2RKF4700X | Volume Production | Digi-Key | P470LCT-ND | 0.1 | 0.1
| 100 | 100 0402 | R7 | 1 | Yageo | RC0402FR-07100RL | Volume Production | Digi-Key | 311-100LRCT-ND | 0.1 | 0.1
| SPST-NO 12V | SWITCH TACTILE SPST-NO 0.05A 12V | SW1 | 1 | ITT C&K | PTS645SM43SMTR92LFS | Volume Production | Digi-Key | CKN9112CT-ND | 0.16 | 0.16
| U/TPS562209 DDCR | IC REG BUCK ADJ 2A TSOT23-6 | U1 | 1
| 3.3V | 3.3 volt fixed regulator, 800mA | U2 | 1 | STMicroelectronics | LD1117S33TR | Volume Production | Digi-Key | 497-1242-1-ND | 0.42 | 0.42
| SK6812 MINI | Serial RGB LED SMT5050 | U3, U4, U5, U6, U7, U8, U9, U10, U11, U12 | 10






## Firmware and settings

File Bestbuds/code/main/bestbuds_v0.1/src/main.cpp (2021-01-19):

/*
--------------------------------------
BestBuds Firmware Version 1.0
Date: 12/07/2019
Author: Brad Momberg, Kyle Rodrigues
Firmware Block Diagram: [insert link]
--------------------------------------
Processor: ESP32 
HSPI Pins: 
ADC0_CS = IO4;
ADC1_CS = IO16;
ADC2_CS = IO33;
SCK = IO14
MISO = IO12
MOSI = IO13
https://docs.espressif.com/projects/esp-idf/en/latest/api-reference/peripherals/spi_master.html
*
*/


//---Prebuild Libraries
  #include <Arduino.h>
  #include <FirebaseESP32.h>
  #include <Dps310.h>
  #include <SPI.h>
  #include <Adafruit_NeoPixel.h>
  #include <Adafruit_SSD1306.h>
  #include <Adafruit_GFX.h>
  #include <rom/rtc.h>

  #include <WiFi.h>
  #include <ESPmDNS.h>
  #include <WiFiUdp.h>
  #include <ArduinoOTA.h>

  #include <NTPClient.h>

  #include <EEPROM.h>

//--Custom Libraries
  #include "push_to_firebase.h"     //NEEDS TO BE COMPLETED
  #include "pressure_sensor.h"      //NEEDS TO BE COMPLETED
  #include "ADS7961.h"
  #include "DHTesp.h"
  #include "pH_Sensor.h"
  #include "bitmaps.h"



//---Variables for new devices/rollouts
  const String  customerID = "Genesis";
  const int     roomNumber = 1;
  const String  HarvestID   = "2019-BD-001";  
  const String  plantStrain ="Blue_Dream";
  int deviceNum;
  const String Moisture_Stake_Version = "1.0";  
  const String Module_Firmware_Version = "v1.01";



//---WiFi Objects EP32 DOES NOT LIKE UNDERSCORES!!!
  //Change these for each new router to be set up
  //Home Router
  //#define WIFI_SSID "Pretty Fly For A Wifi-2.4"
  //#define WIFI_PASSWORD "supercarbon"

//Genisis Router
  #define WIFI_SSID "supercarbon-2G"
  #define WIFI_PASSWORD "runner7373"

//---NTP Client Stuff
  //-These objects are used to the the Unix timestamp into the Firebase push stuff.
  //
  WiFiUDP ntpUDP;
  NTPClient timeClient(ntpUDP);
  unsigned long epochTime;

//---Neopixel Variables and Objects
  #define PIN 18 //Neopixel pins
  #define NUMPIXELS   48 // number of pixels
  // Create an array with the current status of the neopixel
  int PixelStatus[3][48];
  // When setting up the NeoPixel library, we tell it how many pixels,
  // and which pin to use to send signals. Note that for older NeoPixel
  // strips you might need to change the third parameter -- see the
  // strandtest example for more information on possible values.
  Adafruit_NeoPixel pixels(NUMPIXELS, PIN, NEO_GRB + NEO_KHZ400);
  #define DELAYVAL 1 // Time (in milliseconds) to pause between pixels



#define EEPROM_SIZE 2048

//---Firebase Objects
  //These variables SHOULD NOT change on each customer rollout
  //
  #define FIREBASE_HOST "https://grow-d8f9a.firebaseio.com"
  #define FIREBASE_AUTH "nRlg3MIM5LZ9AGdqlAsMhwrQ6RPi12UsJr0XsbSa"

  FirebaseData firebaseData;
  FirebaseJson jsonModuleData;  
  FirebaseJson jsonEnviroData;
  FirebaseJson jsonSoilData;
  FirebaseJsonArray jsonArray_SoilMoisture;

//---Function Prototypes
  //
  int connect_Wifi();
  void firebase_Data_Push();     
  void init_ADC();    
  void ADCRead(int ADC_NUM);  
  void NeopixelSetup();        
  void NeopixelWrite();
  void DHTSetup();
  void CheckDHT();
  void ScreenSetup();
  void ScreenUpdate();
  void pHRead();
  void print_reset_reason(RESET_REASON);
  void verbose_print_reset_reason(RESET_REASON);
  void grabChipId();
  void OTA_init();
  void timeStamp_init();
  void timeStamp_grab();

  void readSerialCalibration();
  void mediumMoistureCalibration();
  void getOffsetCalibration();

  double readCelsius(void);
  double readFahrenheit(void);

  void ADCCalibrate_Dry(int ADC_NUM);
  void ADCCalibrate_Wet(int ADC_NUM);

  void pressureSensorRead();

  void readSerial();
  void pHsensorCalibration();
  void pHRead();

  void setDeviceNumber();
  //Bitmaps
  void WIFI_bitmap();
  void pHCal_bitmap();
  void loading_bitmap();
  void temp_bitmap();
  void pressure_bitmap();
  void ADC_bitmap();
  void time_bitmap();
  
  int loading_status; //this is used for the loading bitmap switch case

//---Moisture Sensor Variables
  //---How many moistures stakes are there
  //
  const int NUM_STAKES        =  16;
  const int NUM_ADC_CHANNELS  =  3;
  /*This array gets used in the ADC_MUX_Update function
  The intention is to built out a 2 dimensional array to store the values from the ADC
  The the ADC Mux spits back a SPI packet that includes the channel that was just read and the value of the channel
  In the ADC_Mux_Update() function, the array index will be compared with the ADC channel value to ensure they are in sync
  */
  int Medium_Moisture_Measurements[NUM_STAKES][NUM_ADC_CHANNELS] = {{1,2,3}, {4,5,6}, {7,8,9}, {10,11,12}, {13,14,15}, {16,17,18}, {19,20,21}
                                                                    ,{22,23,24}, {25,26,27},{28,29,30},{31,32,33}, {34,35,36},{37,38,39},{40,41,42},{43,44,45}
                                                                    ,{46,47,48} };


  //The % humidity values of the moisture stake
  int Medium_Moisture_Percentage[NUM_STAKES][NUM_ADC_CHANNELS] = {{1,2,3}, {4,5,6}, {7,8,9}, {10,11,12}, {13,14,15}, {16,17,18}, {19,20,21}
                                                                    ,{22,23,24}, {25,26,27},{28,29,30},{31,32,33}, {34,35,36},{37,38,39},{40,41,42},{43,44,45}
                                                                    ,{46,47,48} };

  //Calibration variables for the dry value (Maximum)
  int Dry_Offset_Calibration[NUM_STAKES][NUM_ADC_CHANNELS] = {{1,2,3}, {4,5,6}, {7,8,9}, {10,11,12}, {13,14,15}, {16,17,18}, {19,20,21}
                                                                    ,{22,23,24}, {25,26,27},{28,29,30},{31,32,33}, {34,35,36},{37,38,39},{40,41,42},{43,44,45}
                                                                    ,{46,47,48} };

  //Calibration variables for the wet value (Maximum)
  int Wet_Offset_Calibration[NUM_STAKES][NUM_ADC_CHANNELS] = {{1,2,3}, {4,5,6}, {7,8,9}, {10,11,12}, {13,14,15}, {16,17,18}, {19,20,21}
                                                                    ,{22,23,24}, {25,26,27},{28,29,30},{31,32,33}, {34,35,36},{37,38,39},{40,41,42},{43,44,45}
                                                                    ,{46,47,48} };

  

//---Pressure Sensor Objects
  //
  
  #define CS_PRESSURE_SENSOR 32           
  Dps310 Dps310PressureSensor = Dps310();
  const int Pressure_CS = 32;      // set SPI SS Pin
  float Dps_Barometric_Pressure;
  float Dps_Temperature;

  

//---Thermocouple ChipSelect
  const int Thermocouple_CS = 17;      // set SPI SS Pin
  double medium_Temperature; //store the vaue

//---MAX6675 Thermocouple Varibles
  uint16_t RawTemperature;
  const int TempOffSet = -3;

//Debug Function Variables  
  uint64_t chipID_short, chipid; 
  #define uS_TO_S_FACTOR 1000000  /* Conversion factor for micro seconds to seconds */

//---pH Variables
 //See pH_sensor.h

//------DHT variables
  float DHT_airTemperature, DHT_relativeHumidity;
  DHTesp dht;


//---OLED Definitions and Object
  #define SCREEN_WIDTH 128 // OLED display width, in pixels
  #define SCREEN_HEIGHT 64 // OLED display height, in pixels
  #define OLED_RESET     1 // // Wemo SCL 
  Adafruit_SSD1306 display(SCREEN_WIDTH, SCREEN_HEIGHT, &Wire, OLED_RESET);



unsigned long upTime_Timer=0;
                              //Minutes * Seconds * Milliseconds
unsigned long upTime_MaxDuration = 10 * 60 * 1000;

struct sensors {
  bool isPresent = false;
  float value;
};

struct sensors phProbe;
struct sensors thermoCouple;


void setup() {
  Serial.begin(115200);
  delay(200);
  //Init Neopixel
  pixels.begin(); // INITIALIZE NeoPixel strip object (REQUIRED)
  NeopixelSetup();// Load Default Values into NeoPixel strip 
  

  //---EEPROM Initialization
  EEPROM.begin(EEPROM_SIZE);

  //initialise the instance of the SPIClass attached to HSPI 
  hspi = new SPIClass(HSPI);   //initialise hspi
  hspi->begin();
  pinMode(ADC0_CS, OUTPUT); //HSPI SS for ADC#
  pinMode(ADC1_CS, OUTPUT); //HSPI SS for ADC#
  pinMode(ADC2_CS, OUTPUT); //HSPI SS for ADC#
  
  //Thermocouple ChipSelect
  pinMode(Thermocouple_CS, OUTPUT);
  digitalWrite(Thermocouple_CS, HIGH);

  setDeviceNumber();
 
  //OLED Screen Setup
  ScreenSetup();
  delay(10);

  pinMode(CS_PRESSURE_SENSOR, OUTPUT);
 // Serial.println("HSPI Setup Complete");

  //Pressure Sensor 
  Dps310PressureSensor.begin(*hspi, CS_PRESSURE_SENSOR);
  pinMode(Pressure_CS, OUTPUT);
  digitalWrite(Pressure_CS, HIGH); 

  delay(100);

  int WiFi_Connect_Attempts = 0;
  int WiFi_Connect_Max_Attempts = 6;
  WIFI_bitmap();
   do{
      connect_Wifi();
      WiFi_Connect_Attempts++;
      if(WiFi_Connect_Attempts > WiFi_Connect_Max_Attempts){
          Serial.println("--- WIFI CONNECTION FAILED---RESTARTING DEVICE---");
          ESP.restart();
      }
  }while(WiFi.status() !=  WL_CONNECTED);

  loading_bitmap();

  //OTA_init() cannot be removed. Without it, we won't be able to publish another update
  OTA_init();

  delay(100);

  //SPACE RESERVED FOR SCREEN SPLASH
  /*The screen splash is only going to be triggered if the device reset cause is not a software reset*/
  delay(100);
  

  init_ADC();
  delay(100);

  DHTSetup();
  delay(100);


  readSerialCalibration(); 

  getOffsetCalibration();

  /*Improve this function by causing it to read multiple samples over a period of time and average the results*/
  if(phProbe.isPresent){
      pHCal_bitmap();
      pHRead(); 
      delay(500);    
  }

  if(thermoCouple.isPresent){
      temp_bitmap();
      medium_Temperature = readCelsius();
      if(isnan(medium_Temperature)){
        medium_Temperature = 0;
        Serial.println("Medium Temperature out of bounds. \t Setting 0");
      }
  }
  /*The check DHT function will be improved by building it into the firebase_Data_Push function
  We will be calling CheckDHT and passing the temperature values directly*/
  pressure_bitmap();
  CheckDHT();  
  delay(500);

  pressureSensorRead();

  /*This function should be improved by adding averaging to the results sampled*/
  ADC_bitmap();
  Serial.println("---ADC Saple run 1---");
  ADCRead(ADC0_CS); 
  ADCRead(ADC1_CS);
 // ADCRead(ADC2_CS);
  delay(100);

  //Added for testing on 11/26/2019
  //Attempting to fix bug #16
  Serial.println("---ADC Sample Run 2---");
  ADCRead(ADC0_CS); 
  ADCRead(ADC1_CS);
  delay(100);

  /*Neopixel write*/
  Serial.println("Neopixel Write");
  NeopixelWrite(); 


  /*This function contains the offset for the timezone stuff*/
   Serial.println("Fetching Time Stamp");
  time_bitmap();
  timeStamp_init();
  timeStamp_grab();

  /* Firebase write*/
  //Pushing to firebase should be the last thing we do.
  //Because it's pretty much the last functional part of the program
  firebase_Data_Push();  

  upTime_Timer = millis();
  
}


void loop() {

  ArduinoOTA.handle();

  /*We should create a function to loop around and update the OLED display with info
  This will give the customer the impression that the device is doing things when it's
  not actually sending off samples to Firebase*/
  ScreenUpdate();

  if(phProbe.isPresent)
      pHRead();

  if(thermoCouple.isPresent){
      medium_Temperature = readCelsius();
      if(isnan(medium_Temperature)){
        medium_Temperature = 0;
        Serial.println("Medium Temperature out of bounds. \t Setting 0");
      }
  }

  //Added for testing on 11/6/2019
  ADCRead(ADC0_CS); 
  ADCRead(ADC1_CS);
  //ADCRead(ADC2_CS);
  delay(100);

  NeopixelWrite();

 // Serial.print("Medium Reading %: "); Serial.println(Medium_Moisture_Measurements[0][0]);

  Serial.print("Uptime (s): ");       Serial.print(millis()/1000);
  Serial.print(" of: "); Serial.println( (upTime_Timer+upTime_MaxDuration) / 1000 );
  delay(5000);  



  if(upTime_Timer + upTime_MaxDuration < millis()){
    Serial.print("---Device Restarting---");
    ESP.restart();
  }

}


//Make the  function more robust by having it run through for up to 30 seconds before exiting
int connect_Wifi(){
  int wifi_stat_bar = 0;
  uint16_t currentMillis = millis();
  uint16_t timerMaxDuration = 15000;

    WiFi.begin(WIFI_SSID, WIFI_PASSWORD);
    Serial.print("Connecting to Wi-Fi");
    while (WiFi.status() != WL_CONNECTED)
    {
        Serial.print(".");
        /*
        if(wifi_stat_bar<128){
        display.fillRect(0, 0, wifi_stat_bar, 15, WHITE);
        display.display();
        wifi_stat_bar++;
        }*/
        delay(300);
        if(currentMillis + timerMaxDuration < millis()){
          Serial.println("WiFi Connection Failed: Timeout");
          break;
          return 0;
        }
    }
    Serial.println();
    Serial.print("SSID: ");
    Serial.println(WiFi.SSID());
    Serial.print("Signal Strenght: ");
    Serial.print(WiFi.RSSI());
    Serial.println(" RSSI");
    Serial.print("Connected with IP: ");
    Serial.println(WiFi.localIP());
    Serial.println();

    return 1;
}

//This is a test function
void firebase_Data_Push(){

  //#######---WiFi and Firebase setup
    //
    Firebase.begin(FIREBASE_HOST, FIREBASE_AUTH);
    Firebase.reconnectWiFi(true);

   // String path_1 = "firmware_testing/11_11/"; //This path is used for testing purposes...Change the date whenever working with this function
  //  String path_1 = "Firmware_Testing/11_28/"; //This path is used for testing purposes...Change the date whenever working with this function
  // String path_1 = "Firmware_testing/12_04/";
    String path_2 = customerID + "/" + plantStrain + "/" + roomNumber + "/" + deviceNum + "/";
    String path_3 = HarvestID + "/" + epochTime;    


    jsonArray_SoilMoisture.addInt(Medium_Moisture_Percentage[0][0]).addInt(Medium_Moisture_Percentage[1][0]).addInt(Medium_Moisture_Percentage[2][0]).addInt(Medium_Moisture_Percentage[3][0])
      .addInt(Medium_Moisture_Percentage[4][0]).addInt(Medium_Moisture_Percentage[5][0]).addInt(Medium_Moisture_Percentage[6][0]).addInt(Medium_Moisture_Percentage[7][0])
      .addInt(Medium_Moisture_Percentage[8][0]).addInt(Medium_Moisture_Percentage[9][0]).addInt(Medium_Moisture_Percentage[10][0]).addInt(Medium_Moisture_Percentage[11][0])
      .addInt(Medium_Moisture_Percentage[12][0]).addInt(Medium_Moisture_Percentage[13][0]).addInt(Medium_Moisture_Percentage[14][0]).addInt(Medium_Moisture_Percentage[15][0])
      .addInt(Medium_Moisture_Percentage[0][1]).addInt(Medium_Moisture_Percentage[1][1]).addInt(Medium_Moisture_Percentage[2][1]).addInt(Medium_Moisture_Percentage[3][1])
      .addInt(Medium_Moisture_Percentage[4][1]).addInt(Medium_Moisture_Percentage[5][1]).addInt(Medium_Moisture_Percentage[6][1]).addInt(Medium_Moisture_Percentage[7][1])
      .addInt(Medium_Moisture_Percentage[8][1]).addInt(Medium_Moisture_Percentage[9][1]).addInt(Medium_Moisture_Percentage[10][1]).addInt(Medium_Moisture_Percentage[11][1])
      .addInt(Medium_Moisture_Percentage[12][1]).addInt(Medium_Moisture_Percentage[13][1]).addInt(Medium_Moisture_Percentage[14][1]).addInt(Medium_Moisture_Percentage[15][1])
    ;

    //---OLD CODE
    // jsonEnviroData.addDouble("Air_temp", DHT_airTemperature).addDouble("Relative_Humidity", DHT_relativeHumidity).addDouble("Baro_Pressure", Dps_Barometric_Pressure);
    //Check to see if the values grabbed from the DHT are real numbers, if they're not: Send NaN to Firebase;
    if(isnan(DHT_airTemperature)){
       jsonEnviroData.addDouble("Air_temp", 0);
       Serial.println("Dps Air Temperature: NAN. \tSetting 0");
     }
      else{
        jsonEnviroData.addDouble("Air_temp",DHT_airTemperature);
      }

    if(isnan(DHT_relativeHumidity)){
      jsonEnviroData.addDouble("Relative_Humidity", 0);
       Serial.println("DHT Air Humidity: NAN. \tSetting 0");
      }
      else{
          jsonEnviroData.addDouble("Relative_Humidity",DHT_relativeHumidity);
      }

    if(isnan(Dps_Barometric_Pressure)){
      jsonEnviroData.addDouble("Baro_Pressure", 0);
       Serial.println("Dps Baro Pressure: NAN. \tSetting 0");
      }
      else{
        jsonEnviroData.addDouble("Baro_Pressure", Dps_Barometric_Pressure);
      }


    jsonSoilData.addArray("Medium_Moisture", &jsonArray_SoilMoisture);  

    if(thermoCouple.isPresent){
      temp_bitmap();
      double medium_Temperature = readCelsius();
      if(isnan(medium_Temperature)){
        medium_Temperature = 0;
        Serial.println("Medium Temperature out of bounds. \t Setting 0");
      }
        jsonSoilData.addDouble("Medium_Temp",medium_Temperature);
      }
      else{
        Serial.println("-Firebase Push- Medium thermocouple not present on device");
      }

    if(phProbe.isPresent){
        if(isnan(pH_sensor_value))
          pH_sensor_value = 0;
      jsonSoilData.addDouble("Medium_pH", pH_sensor_value);
      }
      else{
        Serial.println("-Firebase Push- pH probe not present on device");
      }

    jsonModuleData.clear().addJson("Enviro_Data",&jsonEnviroData).addJson("Medium_Data",&jsonSoilData);

    //if (Firebase.setJSON(firebaseData, path_1 + path_2 + path_3, jsonModuleData))
    if (Firebase.setJSON(firebaseData, path_2 + path_3, jsonModuleData))
    {
        Serial.println("PASSED");
        Serial.println("PATH: " + firebaseData.dataPath());
        Serial.println("TYPE: " + firebaseData.dataType());
    }
    else
    {
        Serial.println("FAILED");
        Serial.println("REASON: " + firebaseData.errorReason());
        Serial.println("------------------------------------");
        Serial.println();
    }
    //#######---WiFi and Firebase set up and testing routine complete
}

//----------Neopixel---------------
void NeopixelSetup(){
  for (int i = 0; i < NUMPIXELS; i++)
  {
    PixelStatus[0][i] = 0;   //set default red value to 0
    PixelStatus[1][i] = 50;  //set default green value to 10
    PixelStatus[2][i] = 10;   //set default blue value to 0
  }

  pixels.clear(); // Set all pixel colors to 'off'
  pixels.show();
  delay(DELAYVAL);
  
}

void NeopixelWrite() {
 
  int MOISTURE_THRESHOLD = 1000;
  //This function checks for missing stakes
  for(int i = 0; i < 16; i++){
    if(Medium_Moisture_Measurements[i][0] < MOISTURE_THRESHOLD ){
      Serial.print("Pixel "); Serial.print(i); Serial.println(" - No Stake");
      pixels.setPixelColor(i, pixels.Color(0,50,0));
    } else
    {
      Serial.print("Pixel "); Serial.print(i); Serial.println(" - Stake Present");
      pixels.setPixelColor(i, pixels.Color(0,0,0));
    }
      portDISABLE_INTERRUPTS();      // Neopixel timing workaround
      pixels.show();   // Send the updated pixel colors to the hardware.
      portENABLE_INTERRUPTS();
      delay(DELAYVAL); // Pause before next pass through loop
   }

     for(int i = 16; i < 32; i++){
    if(Medium_Moisture_Measurements[i-16][1] < MOISTURE_THRESHOLD ){
      Serial.print("Pixel "); Serial.print(i); Serial.println(" - No Stake");
      pixels.setPixelColor(i, pixels.Color(0,50,0));
    } else
    {
      Serial.print("Pixel "); Serial.print(i); Serial.println(" - Stake Present");
      pixels.setPixelColor(i, pixels.Color(0,0,0));
    }
      portDISABLE_INTERRUPTS();      // Neopixel timing workaround
      pixels.show();   // Send the updated pixel colors to the hardware.
      portENABLE_INTERRUPTS();
      delay(DELAYVAL); // Pause before next pass through loop
   }
     /*for(int i = 0; i < 16; i++){

      if(Medium_Moisture_Percentage[i][1] < MOISTURE_THRESHOLD){
      //Serial.print("Pixel "); Serial.print(i); Serial.println(" active");
      pixels.setPixelColor(i, pixels.Color(0,50,0));
      portDISABLE_INTERRUPTS();     // Neopixel timing workaround
      pixels.show();   // Send the updated pixel colors to the hardware.
      portENABLE_INTERRUPTS();

    delay(DELAYVAL); // Pause before next pass through loop
    //delayMicroseconds(DELAYVAL);
    }
  }

  /*for(int i = 16; i < 32; i++){

      if(Medium_Moisture_Percentage[i-16][1] < MOISTURE_THRESHOLD){
      //Serial.print("Pixel "); Serial.print(i); Serial.println(" active");
      pixels.setPixelColor(i, pixels.Color(0,50,0));
      portDISABLE_INTERRUPTS();     // Neopixel timing workaround
      pixels.show();   // Send the updated pixel colors to the hardware.
      portENABLE_INTERRUPTS();

    delay(DELAYVAL); // Pause before next pass through loop
    //delayMicroseconds(DELAYVAL);
    }
  }*/
  Serial.println("Neopixels updated");
}
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

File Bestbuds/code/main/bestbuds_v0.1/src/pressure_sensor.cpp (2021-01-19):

/*#######---Notes---#######
10.14.2019 - We need to swap to using the HSPI library. If that doesn't work, built it outselves.
*/


#include <Dps310.h>

//#define pin_CS 22  

int16_t pin_CS = 22;

Dps310 Pressure_Sensor = Dps310();


//#######---Initialize the Dps310 Barometric Pressure sensor
//
void init_Pressure_Sensor(){
    pinMode(pin_CS, OUTPUT);
    Pressure_Sensor.begin(SPI, pin_CS);

    Serial.println("Pressure Sensor Initialized");
}

//#######---A function that returns the temperature value of the Dps310 Pressure Sensor
//
float pressure_sensor_temperature(){
    Serial.print("---Temperature---");

    float temperature;
    int ret, oversample = 7;

    ret = Pressure_Sensor.measureTempOnce(temperature, oversample);

   //Serial.println(Pressure_Sensor.getProductId());
   int productu_ID = Pressure_Sensor.getProductId();
   Serial.print("Product id: "); Serial.println(productu_ID);

    Serial.print("\t Ret Val: "); Serial.print(ret);
    Serial.print("\t Temp: ");      Serial.println(temperature);
    return temperature;
}


//#######---A function that returns the barometrics pressure value of the Dps310 Pressure sensor
//
float pressure_sensor_barometric(){
    Serial.print("---Pressure---\t");

    float barometric;
    int ret, oversample = 7;

    ret = Pressure_Sensor.measurePressureOnce(barometric, oversample);

    Serial.print("\t Ret Val: "); Serial.print(ret);
    Serial.print("\t Pressure: ");  Serial.println(barometric);
    
    
    return barometric;
}

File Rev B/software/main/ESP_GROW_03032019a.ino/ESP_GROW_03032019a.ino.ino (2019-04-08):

/*ESP-Grow
By Kyle Rodrigues
Date: 03032019

**Note: This code works, but soil refresh rate is buggy. need to edit logic flow

DHT22 - D4 pin 2
Screen - OLED Screen , Addr 0x3C, character uses 5x5 pixels, (X,Y)
soil capacitive sensor A0

Changes: title change to esp-grow
-oled delays changed from 1000 to 100
-DHT if statement >1000 from >2000
-map function applied to moisture
03032019
- MicroOLED fucntion removed, added 0.96" OLED 
- DHT22 humidity added to screen reading
*/

//****Include Statements******
//ESP8266
#include <ESP8266WiFi.h>
#include <WiFiClient.h>
#include <ESP8266WebServer.h>
#include <ESP8266mDNS.h>

//OLED Screen
#include <Wire.h>  // Include Wire if you're using I2C
#include <Adafruit_GFX.h>
#include <Adafruit_SSD1306.h>

//DHT22
#include "DHT.h"


//*****OLED 0.96" **********
#define SCREEN_WIDTH 128 // OLED display width, in pixels
#define SCREEN_HEIGHT 64 // OLED display height, in pixels
#define OLED_RESET     1 // // Wemo SCL 
Adafruit_SSD1306 display(SCREEN_WIDTH, SCREEN_HEIGHT, &Wire, OLED_RESET);

//*****DHT22 **********
#define DHTPIN 2     // what digital pin the DHT22 is conected to
#define DHTTYPE DHT22   // there are multiple kinds of DHT sensors
DHT dht(DHTPIN, DHTTYPE);
int timeSinceLastRead = 0;

//*****ESP8266 **********
const char* ssid = "Pretty Fly For A Wifi-2.4";
const char* password = "supercarbon";
ESP8266WebServer server(80);

void handleRoot() {
	server.send(200, "text/bold", "ESP-Grow");
}

void handleNotFound() {
	String message = "File Not Found\n\n";
	message += "URI: ";
	message += server.uri();
	message += "\nMethod: ";
	message += (server.method() == HTTP_GET) ? "GET" : "POST";
	message += "\nArguments: ";
	message += server.args();
	message += "\n";
	for (uint8_t i = 0; i < server.args(); i++) {
		message += " " + server.argName(i) + ": " + server.arg(i) + "\n";
	}
	server.send(404, "text/plain", message);
}

void setup(void) {
	Serial.begin(115200);
 
    //******OLED Start*****
   // SSD1306_SWITCHCAPVCC = generate display voltage from 3.3V internally
  if(!display.begin(SSD1306_SWITCHCAPVCC, 0x3C)) { // Address 0x3D for 128x64
    Serial.println(F("SSD1306 allocation failed"));
    for(;;); // Don't proceed, loop forever
  }
    display.display();
    delay(2000); // Pause for 2 seconds
  // Clear the buffer
  display.clearDisplay();
	Serial.println("Running OLED");
 
	Serial.println("Running Wifi!");
	WiFi.mode(WIFI_STA);
	WiFi.begin(ssid, password);
	Serial.println("");


	// Wait for connection
	while (WiFi.status() != WL_CONNECTED) {
		delay(500);
		Serial.print(".");
		display.clearDisplay();
    display.setTextSize(1);             // Normal 1:1 pixel scale
    display.setTextColor(WHITE);        // Draw white text
		display.setCursor(10, 0); // Set cursor to top-left
    display.cp437(true);         // Use full 256 char 'Code Page 437' font
		// Print can be used to print a string to the screen:
		display.println("Girl Scout Cookies");
		display.display();       // Refresh the display
		delay(100);          // Delay a second and repeat
		display.setCursor(40, 15);
		display.println("Get WIFI");
		display.display();
    delay(100);
     
	}
 
	Serial.println("");
	Serial.print("Connected to ");
	Serial.println(ssid);
	Serial.print("IP address: ");
	Serial.println(WiFi.localIP());
 
  display.clearDisplay();
  display.display();
  delay(100);
  display.setCursor(10, 0); // Set cursor to top-left
  display.println("Girl Scout Cookies");
  display.setCursor(35, 15);
	display.println(WiFi.localIP());
	display.display();
	delay(100);
  display.display();

	if (MDNS.begin("esp8266")) {
		Serial.println("MDNS responder started");
	}

	server.on("/", handleRoot);

	server.on("/inline", []() {
		server.send(200, "text/plain", "this works as well");
	});

	server.onNotFound(handleNotFound);

	server.begin();
	Serial.println("HTTP server started");

}

void loop(void) {
  DHT22Sens();
	moist();
  screen();
	server.handleClient();
	delay(1000);

}

//This function was made to easily clear the screen and readd title and ipaddr
void screen(void){
  display.clearDisplay();
  display.setCursor(10, 0);
  display.cp437(true);         // Use full 256 char 'Code Page 437' font
  display.println("Girl Scout Cookies");
  display.setCursor(35, 15);
  display.println(WiFi.localIP()); 
  DHT22value();
  
}

void moist() {
	int mositsens = map(analogRead(0),320,750,100,0);
	Serial.println(mositsens);
 	display.setCursor(0, 30);
  display.println("Soil:");  
  display.setCursor(35, 30);
	display.println(mositsens);  
  display.setCursor(50, 30);
  display.println("%");
	display.display();
	delay(1000);
  display.display();
	timeSinceLastRead += 100;
}

void DHT22Sens() {

	if (timeSinceLastRead > 1000) {
		// Reading temperature or humidity takes about 250 milliseconds!
		// Sensor readings may also be up to 2 seconds 'old' (its a very slow sensor)
		float h = dht.readHumidity();
		// Read temperature as Celsius (the default)
		float t = dht.readTemperature();

		// Check if any reads failed and exit early (to try again).
		if (isnan(h) || isnan(t)) {
			Serial.println("Failed to read from DHT sensor!");
			timeSinceLastRead = 0;
			return;
		}
		float hic = dht.computeHeatIndex(t, h, false);

//		Serial.print("Humidity: ");
//		Serial.print(h);
//		Serial.print(" %\t");
//		Serial.print("Temperature: ");
//		Serial.print(t);
//		Serial.print(" *C ");
//		Serial.print("Heat index: ");
//		Serial.print(hic);
//		Serial.print(" *C ");

		timeSinceLastRead = 0;
	}
}

 //This holds the current value of the DHT22 from the last read
    void DHT22value (void){
      display.setCursor(0, 40);
      display.println("DHT22:");
      display.setCursor(35, 40);
      display.println(dht.readTemperature());
      display.setCursor(70, 40);
      display.println("oC");
      display.setCursor(35, 50);
      display.println(dht.readHumidity());
      display.setCursor(70, 50);
      display.println("%");
      display.display();
      delay(100);          // Delay a second and repeat
      display.display();
}

void webupdate(){
  

}

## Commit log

2019-02-18 Adding current progress sofar
2019-04-28 Altium PCB Files Added
    [ESP_Grow_Rev_A.PcbDoc, ESP_Grow_Rev_A.PrjPCB, ESP_Grow_Rev_A.SchDoc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]
2019-04-29 updated pcb into two separate ones
    [ESP-Grow_OLED_Rev_A.PcbDoc, ESP-Grow_OLED_Rev_A.PrjPCB, ESP-Grow_OLED_Rev_A.SchDoc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]
2019-05-03 project separated into two pcb
    [ESP-Grow_OLED_Rev_A.PcbDoc, ESP-Grow_OLED_Rev_A.PrjPCB, ESP-Grow_OLED_Rev_A.SchDoc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]
2019-05-03 pcbs ordered for oled pcb
    [ESP-Grow_OLED_Rev_A.PcbDoc, ESP-Grow_OLED_Rev_A.PrjPCB]
2019-05-03 working on main pcb
    [ESP-Grow_OLED_Rev_A.PrjPCB, ESP_Grow_Main_Rev_A.PcbDoc, ESP_Grow_Main_Rev_A.SchDoc]
2019-05-04 layer stackup added
    [ESP_Grow_Main_Rev_A.PcbDoc]
2019-05-04 5v and 3v added to pcb
    [ESP-Grow_OLED_Rev_A.PrjPCB, ESP_Grow_Main_Rev_A.PcbDoc, ESP_Grow_Main_Rev_A.PrjPCB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]
2019-05-04 layout update
    [ESP_Grow_Main_Rev_A.PcbDoc, ESP_Grow_Main_Rev_A_1_Con.SchDoc, ESP_Grow_Main_Rev_A_2_3V_5V.SchDoc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]
2019-05-05 layout almost done
    [ESP_Grow_Main_Rev_A.PcbDoc]
2019-05-05 top silk updated with rev name
    [ESP-Grow_OLED_Rev_A.PcbDoc, ESP_Grow_Main_Rev_A.PcbDoc]
2019-05-05 polygons added
    [ESP-Grow_OLED_Rev_A.PcbDoc, ESP_Grow_Main_Rev_A.PcbDoc]
2019-05-07 neopixel and sonar pins added
    [ESP_Grow_Main_Rev_A.PcbDoc, ESP_Grow_Main_Rev_A_1_Con.SchDoc]
2019-05-11 pcb update
    [ESP-Grow_OLED_Rev_A.1.PcbDoc, ESP-Grow_OLED_Rev_A.1.PrjPCB, ESP-Grow_OLED_Rev_A.1.SchDoc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]
2019-05-18 testing code changes
    [ESP_Grow_Main_Rev_A_1_Con.SchDoc]
2019-05-19 Gerbers sent to JLCPCB for fab
    [ESP_Grow_Main_Rev_A.PcbDoc, ESP_Grow_Main_Rev_A.PrjPCB, ESP_Grow_Main_Rev_A_1_Con.SchDoc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]
2019-05-19 send OLED and Main PCB for fab
    [ESP-Grow_OLED_Rev_A.1.GBL, ESP-Grow_OLED_Rev_A.1.GBO, ESP-Grow_OLED_Rev_A.1.GBS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]
2019-05-25 BOM added
    [ESP_Grow_Main_Rev_A.xlsx]
2019-05-25 updated bom
2019-05-27 BOM updated
    [ESP_Grow_Main_Rev_A-5252019.xlsx, ESP_Grow_Main_Rev_A.xlsx]
2019-05-30 fixed dht22/11 code
    [ESP_Grow_Main_Rev_A-5252019.xlsx, ESP_Grow_Main_Rev_A.DXF, ESP_Grow_Main_Rev_A.PcbDoc]
2019-06-02 Changing project status to Rev B
    -Bugs found in Rev A layout
    changing to Rev B
    -see altium change log in Rev B
    [ESP-Grow_OLED_Rev_A.1.GBL, ESP-Grow_OLED_Rev_A.1.GBO, ESP-Grow_OLED_Rev_A.1.GBS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]
2019-06-06 updated project with newer pcb files from archive
    [ESP-Grow_OLED_Rev_A.1.PcbDoc, ESP_Grow_Main_Rev_B.PcbDoc, ESP_Grow_Main_Rev_B.PrjPCB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]
2019-06-18 major code update, see 6-17-2018
    [ESP_Grow_Main_Rev_A_Keepout.DXF]
2019-07-16 working code - 7-15-2019
    [ESP-Grow_OLED_Rev_A.1.GBL, ESP-Grow_OLED_Rev_A.1.GBO, ESP-Grow_OLED_Rev_A.1.GBS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]
2019-08-01 updated platform io
    [ESP_Grow_Main_Rev_A.xlsx]
2019-10-15 working code
    [ESP_Grow_Main_Rev_A.PrjPCB]
2019-11-16 updated a max pump counter
2019-12-15 starting rev b
    [ESP_Grow_Main_Rev_B.PrjPCB, ESP_Grow_Main_Rev_B_0_Title.SchDoc, ESP_Grow_Main_Rev_B_1_CPU.SchDoc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]
2020-03-21 fixed issue with serial crashing when starting oled screen
    changed OLED_RESET from 1 to -1
    [main.cpp]
2020-03-22 added pump calibration into serial input
2020-03-25 added RSSI and fixed pump setpoinnt
    [main.cpp]
2020-03-28 updating buttons
    [ESP_Grow_Main_Rev_B_3.SchDoc]
2020-04-04 added separate wet /dry calibration
